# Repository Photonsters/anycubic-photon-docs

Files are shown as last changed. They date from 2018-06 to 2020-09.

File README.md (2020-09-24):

# Anycubic Photon Owner's Documentation

Use this repository to collect information on the Anycubic Photon LCD resin printer's hardware, software and usage. 

**IMPORTANT NOTE!**

**As of September 2019, Anycubic has been shipping printers which deceptively look like original Photon printers but are not. These new printers (commonly called the Fauxton) have new motherboards (PTB2BK) and are incompatible with the original Photon printers. The information provided here for the most part will not apply to this new printer.** 

**Please also note that most of the community tools, software, mods and information here do NOT apply to the new Fauxton or the Photon-S model. They are fundamentally different printers.** 

Want to help? Check at the bottom of this page for the [TO DO](#todo) list and open a [issue with #IWantToHelp.](https://github.com/Photonsters/anycubic-photon-docs/issues/new?title=IWantToHelp)

## Table of Contents

* [Frequently asked questions (FAQ)](FAQ.md)
* [Known issues](known-issues/photon-known-issues.md)
* [Photon technical specifications](#photon-technical-specifications)
* [Photon file image format](#photon-file-image-format)
* [Photon slicing software](#photon-slicing-software)
* [Community resin exposure settings](#community-resin-exposure-settings)
* [Community projects](#community-projects)
* [Community Mods](#user-mods-on-facebook)
* [Social media groups](#social-media-groups)
* [Models, Photon Blueprints & Resources](#models--resources)
* [Firmware Archives](/firmware/README.md)
* [TO.DO.](#todo)

<!-- toc -->

## Frequently asked questions (FAQ)
[Check the FAQ page](FAQ.md) before asking questions! You may find the answers to all your questions regarding setting up your Photon, to post processing your prints, already covered in the FAQ. 

## Known issues
There are several known issues with the Photon hardware and software. [Check the known issues page](known-issues/photon-known-issues.md) for details, solutions and workarounds.

## Photon technical specifications
#### Dimensions
- Machine Volume: 220(L)x200(W)x400(H)
- Print Volume: 115(L)x65(W)x155(H)
- Empty Vat weight 630g [(FB Link)](https://www.facebook.com/groups/AnycubicPhoton/permalink/1644848155659820/)

#### Photon masking
- RGB 5.5 MIPI_DSI 2K LCD screen [(Sharp LS055R1SX03)](https://github.com/Photonsters/anycubic-photon-docs/blob/dev/Temp-resources/LS055R1SX03-SKU958440.pdf) 
- 68.04(W)mm x 120.96(H)mm (5.46")
- XY resolution: 47.25µ (0.04725mm)
- 538ppi
- Color Pixel Arrangement:RGB Vertical Stripe
- Power Supply Voltage:AVDD=5.5+/-0.1V AVEE=-5.5+/-0.1 V
- MIPI 5.5 50 Pin 0.4 Pitch connectors: [Screen: WP7B-P050VA1 ; Board: WP7B-S050VA1 - (FB)](https://www.facebook.com/groups/AnycubicPhoton/permalink/1646286412182661/)

#### Motion driver / mechanics
- T8 leadscrew with 2mm lead/pitch
- Nema 17 Motor 1.8º 200steps/rev
- Driver embeded Polulu Alegro 4998 set at 1/16 microstepping
- Hardware resolution 10µ (0.01mm)
- Digital microstepped resolution 0.625µ (0.000625mm) - [Advised reading: Microstepping Myths and Realities](https://tinyurl.com/y92kexf5)

#### Electronics
- LED power 25W 405nm
- PSU 12v 6A (72w) - 5.5 x 2.5mm Jack - [check image](https://user-images.githubusercontent.com/11083514/42894729-92fd1f22-8aaf-11e8-9f58-2fdb9be91fb1.png)

#### Photon file image format
- 2560x1440px 
- Black and White 
- RLE 7bit encoding
- 538 dpi (537.566 dpi)

## Firmware & Configuration files
If you've just received your Photon, or it's working properly, **do not** update your firmware unnecessarily. 
- [Photon official firmware & default gcode](https://github.com/Photonsters/anycubic-photon-docs/tree/master/firmware) (including unofficial releases and gcode mods). Use at own risk. 

## Photon slicing software

#### [ANYCUBIC Photon Slicer](http://www.anycubic3d.com/support/show/594032.html)
Go to [this page](https://www.anycubic.com/) slicer will be shoved under the printer you will have to scroll a bunch.
 
 (https://www.anycubic.com/)

#### [**Chitu Slicer**](http://www.cbd-3d.com/en/soft/dlpslicer.shtml) (ANYCUBIC is rebranded Chitu)
Chitu devs have been helping Photonster devs with some support questions, and Chitu's new software release will allow for better integration of Photonsters tools with the slicer software, and will support many new formats including zip/gcode import/export.

#### [**Chitubox**](https://www.chitubox.com/) (New Slicer for the photon from the same makers of ChituDLP)
New software that integrates code and ideas first seen in the community projects VoxelOps, Validator, Rob's 3D photon Viewer and Photon File Editor Project. 

#### [**Photon Open Slicer**](https://github.com/Photonsters/Slicer) (Community developed OpenSource Slicer)
A independent command line Slicer from Photonsters, that can be integrated with MeshMixer or any other software capable of outputting a STL file. 

#### [List of Slicing Software](https://docs.google.com/spreadsheets/d/1wZFdewMztEp_1RPubQw_8UdIZK7Z2oIWxByVpAPAfXI/edit#gid=0)
Some of the slicers that are available to date.

## Community resin exposure settings
- [Known good resin settings](https://docs.google.com/spreadsheets/d/1crvzMnt_8NJXAsABinoIhcOjE8l3h7s0L82Zlh1vkL8/edit#gid=0) - Curated by Artur Fuste. 
- Also check the resin exposure finder test under community projects below.

## Community resin precision gauge test
[Resin Precision-Fit Test-Gauge](https://docs.google.com/spreadsheets/d/1yDwszgncTyOxvyJho6y1kxLJquH2GsfL83KaFXT6068) - This is for resin as tested with no software profile/compensation. Dimensions can be corrected by activating the horizontal-size compensation feature in your slicing software. If you don't have this feature, please contact your slicer developer.

## Printed material torsion test results
[Torsion Test Results](https://docs.google.com/spreadsheets/d/1JlqLSi4sxZLdA-hHCp6Ow4isoGMNI7nlE9Nmbj1ajWk) - 3D printed material comparison by torsion testing.

## Community projects
- [Resin Exposure Range Finder](https://github.com/altLab/photon-resin-calibration) - Quick method to test multiple resin exposure settings in one go. *(X3msnake)*
- [Photon File Validator](https://github.com/Photonsters/PhotonFileViewer) - Check if your sliced file has errors before printing. *(Bonosoft)*
- [Photon Voxel 3D Viewer](https://github.com/Ordenritterlein/PhotonTool/blob/master/README.md) - Javascript 3D model rebuilder and visualization from sliced Photon files. *(Ordenritterlein / Rob2048)*
- [Photon File Utils - PFE](https://github.com/NardJ/PhotonFileUtils) - Photon file visualizer editor and creator tools. *(NardJ)*
- [PCB2Photon](https://github.com/Reonarudo/pcb2photon) - Swift Gerber image to Photon for PCB mask burning and production. *(Reunarudo)*
- [Photon Go](https://github.com/Andoryuuta/photon) - Library to read and write Photon and .cbddlp files. *(Andoryuuta)*
- [UV light distribution tester](https://www.facebook.com/kzhkshj/posts/1782894801789685)
- [Pixel Dimming Tool](https://github.com/alpet83/PhotonProcessor)*(alpet83)*
- [Photon Open Slicer - POS - Meshmixer Plugin](https://github.com/Photonsters/Slicer) - *(NardJ)*
- [Voxel Ops](https://github.com/Photonsters/VoxelsOps) - Voxel tools to dilate, erode, hollow, project and measure. *(Antharon)*
- [DecreasePixel GUI](https://github.com/Hans2004/Anycubic-Photon-decreasePixel-with-GUI) - Simple erode function. Compensate slices on .photon files to closely fit design dimensions. *(Hans De Jong)*
- [DecreasePixel CLI](https://github.com/Hans2004/AnyCubic-Photon-Decrease-Pixel) - Same as the above but Command Line version. Confirmed working without issue [in a FB post](https://www.facebook.com/groups/AnycubicPhoton/permalink/1835060846638549/) *(Hans De Jong)* 
- [cbddlp - xycompensate](https://github.com/yaqwsx/ElegooMarsUtility) *(yaqwsx)* - [check his blog](https://blog.honzamrazek.cz/)
- [Hexeditor Okteta](https://github.com/Hans2004/okteta-photon) template for .photon format. *(Hans De Jong)*
- [PRUSA SLICER SL1 files to Photon Converter](https://github.com/fookatchu/SL1toPhoton) *(fookatchu)*
- [pyPhotonfile - library for photon file manipulating](https://github.com/fookatchu/pyphotonfile)*(fookatchu)*
- [cbddlp, photon, photonS, pws - File cross converter](https://github.com/Ordenritterlein/PhotonsFileConverter) *(Ordenritterlein)*
- [PNG2Photon - Convert a image to a photon file](https://github.com/0x3f00/PhotonCpp) *(0x3f00)*
- [Photon Timelapser EOS](https://github.com/lagnajeet/PhotonTimeLapse) [video](https://www.youtube.com/watch?v=u1mt8Q_h7qg&list=PLVMKVuHiQBM1TjSq00kHshXuMJEsih7rn&index=18) *(lagnajeet)*
- [Photon Network Controller - Allows to manage files and start prints on any CBD board printer](https://github.com/Photonsters/Universal-Photon-Network-Controller/blob/master/README.md) *(lagnajeet)*
- [Gcode to Images](https://github.com/svsdval/gcode2photon) *svsdval*
- [PhotonPCB - Create printed circuit boards with MSLA](https://github.com/borelg/PhotonPCB) *(borelg)*
- [UV3DP - Multiformat converter command line tool (PHZ,CTB,CBDDLP,CWS(nova),SL1...)](https://github.com/ezrec/uv3dp/blob/master/README.md) *(ezrec)*

- [**#BlackBoaProject** - Photonsters Rebuild Improvement and Documentation of a Photon Classic](https://photos.app.goo.gl/FDa5uVDD6zWR39Wt8)

## User mods (on Facebook)
- [Cheap and easy Heater, PTC Fan and temperature controller](https://www.facebook.com/groups/AnycubicPhoton/permalink/1550627681748535/)
- [PTC Heater and temperature controller V2](https://www.facebook.com/permalink.php?story_fbid=10157191752823680&id=651553679)
- [PTC Heater and temperature controller that prints flat with no support](https://www.thingiverse.com/thing:3412516?fbclid=IwAR2-71wrzMquMxCCqnwgRDSsMIfEYvs9tsWgYu_tbYqgjgc3luOuuhr0QFU) 
- [Printed Universal resin drainer](https://www.facebook.com/groups/AnycubicPhoton/permalink/1508547859289851/)
- Gangsta resin drainers [1](https://www.facebook.com/groups/AnycubicPhoton/permalink/1376704139140891/), [2](https://www.facebook.com/groups/AnycubicPhoton/search/?query=gangsta%20drainer&epa=SEARCH_BOX)
- [Red & Black Acrylic windows with cad files](https://www.facebook.com/groups/AnycubicPhoton/permalink/1367548836723088/)
- [Tuning Photon Z driver or using a external Driver module](https://www.facebook.com/media/set/?set=oa.1350659371745368&type=3)
- [Anycubic Photon Z Axis Modification](https://www.facebook.com/groups/AnycubicPhoton/permalink/1599717403506229/) 
- [IPA Cleaner Station with stir Mixer](https://www.facebook.com/groups/AnycubicPhoton/permalink/1604847169659919/)
- [IPA Classic Cleaning Station](https://www.facebook.com/permalink.php?story_fbid=10157258442468680&id=651553679) 
- [Pi Zero W WiFi Thumb Drive](https://www.facebook.com/groups/AnycubicPhoton/permalink/1610232152454754/)
- [Pi Zero W WiFi Thumb Drive 2](https://www.facebook.com/groups/AnycubicPhoton/permalink/1640913006053335/)
- [NanoDLP Photon Brain Transplant](https://www.facebook.com/groups/AnycubicPhoton/permalink/1657220444422591/) 

**NETWORK ENABLED PHOTON UI**
- [PSHCNET UI in action](https://www.facebook.com/groups/AnycubicPhoton/permalink/1651711838306785/)
- [Network Ready back grill vent](https://www.thingiverse.com/thing:3613864)

**Z AXIS MODS**
- [Dual Rail Solid - skipbaker](https://www.thingiverse.com/thing:3539028/files)
- [Dual Rail Flanges - PhotonHebs](https://www.thingiverse.com/thing:3473868/files)
- [Dual MGN9H Printed - Beezen](https://www.thingiverse.com/thing:3504872)
- [Dual Linear Bearings - danroh](https://www.thingiverse.com/thing:3490431)

## Social media groups
- [Anycubic Photon LCD Printer Owners Group](https://www.facebook.com/groups/AnycubicPhoton/?ref=group_header) on Facebook, with over 10,000 members. 
- [ANYCUBIC Photon Forum](http://photonforum.statusavailable.pt/viewforum.php?f=23), managed by official distributor PT. 
- [Twitter #AnycubicPhoton](https://twitter.com/hashtag/ANYCUBICPHOTON?src=hash)

## Models & resources

### Calibration models
Use these resources to test how your Photon is printing, and to remove guesswork from calculating resin exposure times.
- [X3msnake's Resin Exposure Range Finder](https://github.com/altLab/photon-resin-calibration)
- [ANYCUBIC Photon calibration file By Ilja](https://www.myminifactory.com/object/3d-print-anycubic-photon-calibration-file-70127)
- [Photonia Pixel Perfect Range Tester](https://www.facebook.com/groups/AnycubicPhoton/permalink/1567794123365224/) 
- [Photon LCD mask Boundary Checker](https://www.thingiverse.com/thing:3345921) - A printable test for your mask boundaries, which may vary from printer to printer.
- [Bed of nails UV coverage test](https://www.thingiverse.com/thing:2852334) - A quick test print to check for even UV coverage of your build plate. Useful for full plate prints or models placed close to edges. 
- [Photon LCD defect mapper](https://www.thingiverse.com/thing:3395800) - A quick test print to map LCD dead pixels, and workaround them in your slicer. 
- [Z Wobble quick test](https://www.facebook.com/groups/AnycubicPhoton/permalink/1507962279348409/) - A quick test for Z wobble, or other planar surface anomalies. 

### Photon Cad files and Blueprints
- [Photon Blueprints CAD files on this repo](https://github.com/altLab/anycubic-photon-docs/tree/master/photon-blueprints)
- [Photon on Thingiverse](https://www.thingiverse.com/search?q=Anycubic+Photon)

### Models for Resin Printing
- [DLP/SLA models on MyMiniFactory](https://www.myminifactory.com/search/?tech=DLP_SLA)

### Tutorials, videos, tips & tricks
- [Photonsters Youtube Channel](https://www.youtube.com/channel/UCtkUaPjl49fyaNOLNTbKHlQ)
- [Troubleshooting DLP Prints](https://l3d.ie/2018/06/29/dlp-3d-printing-troubleshooting/)
- [Supports created with Meshmixer](https://youtu.be/OXFKVmMwXCQ?t=2m10s)
- [How supports work](./Resources/AddingSupportsForSLA3DPrinters-v1.pdf)
- [2018 - Resin Casting: A Collection of Hypotheses](http://www.santafesymposium.org/2018-santa-fe-symposium-papers/2018-resin-casting-a-collection-of-hypotheses)
- [How to use Netfabb supports with LCD printers](https://docs.google.com/document/d/1aC4MIkIyjG61bllVglCZ308qukxOhE7jJ9tKQQh0aPY)
- [How LCDs work](www.bitly.com/HOW-LCDS-WORK)
- [The science behind a 3d Printer - Projection, Mask and Resins](https://youtu.be/97ARLiTHjX0)

## TODO
1. Videos for the [Photonsters Youtube Channel](https://www.youtube.com/channel/UCtkUaPjl49fyaNOLNTbKHlQ)
1. Map Photon hardware
1. Map Photon file anatomy
1. How-to test resins
1. How-to level
1. How-to use external Stepper driver
1. Create Repo with resins and community consensus resin test method [check this page](https://github.com/Photonsters/anycubic-photon-docs/blob/master/resin-tests/resin-testing-protocol.md)
1. List official slicers and alternative/usefull software
1. Collect config files and firmware from Google group
1. Collect community reversed Photon CAD parts
1. List community software projects and tools for the Photon
1. Finish compare chart https://ethercalc.org/ResinPrintersCompareChart

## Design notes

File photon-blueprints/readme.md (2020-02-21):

# PHOTON BLUEPRINTS

Serial connection: 115200, 8, n, 1
You can use Putty, Tealterm or Arduino Serial

- Touch - SPI (SCK, SDI, SDO, CS, GND, 5V)
- Touchscreen LCD - Paralell 16bit (D0-D15, RS, WR, RD, CS, GND, 5V)
- [BlackBoa Dissasembly photos and mesures](https://photos.app.goo.gl/FDa5uVDD6zWR39Wt8)

- [CAD model of complete Photon mechanical assembly on GrabCAD](https://grabcad.com/library/photon-3d-printer-assembly-1)

## ICs

Screen Controllers

- XPT2046 or HR2046 (touch - all screens)
- [ILI9341 (2.8")](2.8inches_V3.9_Back_Dimensions.PDF) 
- [ILI9488 (3.5")](3.5inches_V3.9_Back_Dimensions.PDF) 
- [TSC2046 - Touch Digitizer IC](https://www.ti.com/lit/ds/symlink/tsc2046.pdf)

- [TouchScreen Pinouts (KUDOS Cex123)](Photon_Touchscreen_Pinouts.pdf) 
- Touchscreen cable: 40-Pin FFC/FPC Flat Cable Pitch 0.5mm 300mm [Forward Direction](https://user-images.githubusercontent.com/11083514/60126474-fea23a80-9785-11e9-896a-7aaa8cd2b04f.png)

Logic Chips
- [FPGA - Altera EP1C3 Cyclone 1](https://user-images.githubusercontent.com/11083514/60964874-5e631e80-a30c-11e9-8678-4eee115b1eeb.jpg) (responsable for image processing)
- [ARM - STM32F407ZCT6](https://user-images.githubusercontent.com/11083514/60965063-cdd90e00-a30c-11e9-8cb0-f4535a3e73f8.png) (responsible for motion actions and ui)

## OTHER PARTS

- Omron endstop [EE-SX674-WR](https://s.click.aliexpress.com/e/_d6Iysd5)
- Z axis U ballbearings [SG15-2RS](https://s.click.aliexpress.com/e/_d7qVfIT)
- [List of all fastener sizes and threads used on the Photon](https://github.com/Photonsters/anycubic-photon-docs/blob/master/photon-blueprints/Anycubic%20Photon%20Fasteners%20Sheet.xlsx)

#### Confirmed Gcode Commands via Serial:

- M6030 "Photon/AA-TEST-PRINTS/_ShallowAnglesAATest_0X.photon" (starts a print file name imeddiatly)
- M6032 "Photon/AA-TEST-PRINTS/_ShallowAnglesAATest_0X.photon" (Reads a File Into Memory to be started with M6045) R: (file length in bytes)
- M24 (Starts printing the M6032 open file on memory)
- M27 (Report SD print status) (M27 S4 - Report 4 seconds, M27 S0 - Stop reporting, M27 C - Report currently open filename)
- M6045 I4000 "M24" (Waits the Delay set time and Starts Printing the M6032 open file on memory)
- M4001 (returns the configured stepper movement for all axis) R: (X:0.011430 Y:0.011430 Z:0.000625 E:0.001340 T:0/0/0/155/1 U:'GBK' B:1) 
- M105 (returns sensor temperatures) R: (ok T:161 /0 B:164 /0 @:0 B@:0)
- M8512 "configFile.gcode" (Dumps the current config.gcode EEPROM data into a file)
- G28 Z (Home Z Axis)
- G0 Z10 (Move Z axis at max speed)
- G0 Z10 F600 (Move Z axis at F speed)
- M6040 I100 (Reboot I defines the delay before restart)
- M7506 I636264 T0		//0; 1; color_flip, (Changes UI colours Negative/Positive/or switch watever its on)
- M9005 '"Networkname","Password"'
- G90 Absolute Positioning
- G91 Incremental Positioning

[List of WIFI commands taken from ChituClient App](ChituClientWifiProtocol-translated.txt)

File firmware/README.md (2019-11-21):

## ANYCUBIC PHOTON FIRMWARE ARCHIVE 

These are archived firmware images of the Anycubic Photon printer.

Unless there is an issue with your machine or current firmware, it is recommended that you do not unnecessarily update or reflash it. 

**The latest firmware as of October 2019 available from Anycubic's website is v4.2.19. This version is buggy and not recommended. Use v4.2.18 instead.** 

*By downloading and using the archived files, you acknowledge that you are doing so entirely at your own risk.*

[Yes, I understand, show me the files!](https://github.com/Photonsters/anycubic-photon-docs/tree/master/firmware) 

## List of Known Firmware
The stock firmware of most of the first generation blue windowed machines is 4.0.11_LCD. It is the only firmware that did not have the "frame shearing" bug. This bug was finally addressed and fixed on firmware v4.2.18.  

Here is a partial list of known firmware with images as documented on a 
[Facebook post.](https://www.facebook.com/groups/AnycubicPhoton/permalink/1599259826885320/)

---

## General Instructions

- Copy the 3 files (sometimes only 2) to the USB root folder.
- On startup the update.lcd file will be used to update the firmware and the printer will start and then beeps.
- At this point, navigate via the touchscreen menu to the choose and "print" the other file(s), consecutively.  
- Once done, safely shutdown and **delete the firmware files** from your usb stick. 
- Now you can restart the printer. 

If the menu shows a T_88 error code, this means that the firmware files were not coherent.
Check in the menu if the version has been updated to the correct firmware version, if so you can "print" the other two files again.

---

## Photon GCode Commands 

Big thanks to Master Johnson Yeh for putting this together.

*Translated text:*

After getting the Chinese version of the gcode parameter description, let me know better that the experiment I did before is correct.

If you want to control the relevant parameters of the Z axis, the following parameters can be used together with the application.

M8070 S3 is set to the slow rise Z distance height of the release type.

M8070 Z6 is the total height of the Z release type = S# slow rise Z distance height + fast rise distance height, so the height of 6-3=3 rapid rise is 3mm

M8015 T2 is the speed of Z-axis slow release
M8016 T3 is the rapid rise and rapid descent speed of Z-axis release. This parameter speed controls the speed of rapid rise and rapid decline.

I would like to suggest that Anycubic should add a new parameter to control the falling speed parameter.

After finalizing the settings, you need to save the parameters you designed to the device using the M8500 parameters.

My last test parameter was parameter(Slow T1).gcode changed as follows:

M8015 T1;

M8016 T2;

M8070 Z6;

M8080 S3;

M8500 ;

*Original text:*

取得中文版gcode參數說明後, 讓我更明白之前做的實驗是正確的.
如果要控制Z軸的相關參數有下列幾個參數是可以搭配應用的.

M8070 S3 是設定離型的慢速上升Z距離高度
M8070 Z6 是Z離型總高度 = S#慢速上升Z距離高度+快速上升距離高度, 所以6-3=3快速上升的高度為3mm

M8015 T2 是Z軸慢速離型上升的速度
M8016 T3 是Z軸離型快速上升及快速下降速度, 這個參數速度控制著快速上升跟快速下降的速度

我想建議 Anycubic 應該新增加一個參數在控制下降的速度參數.

最後完成設定後, 需要使用Ｍ8500參數將您所設計的參數保存到設備內.

我上一次測試參數是 parameter(Slow T1).gcode 更改的內容如下:

M8015 T1
M8016 T2

M8070 Z6
M8080 S3

M8500

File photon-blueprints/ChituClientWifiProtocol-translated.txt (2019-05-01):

G:\yiyu\workspace\software_v3_V1.2.30\software_v3_V1.2.30\software_v3\DOC\赤兔主板-wifi通信协议-wifi-protocal.txt 26 November 2016 16: 35
Author: Yi Yu last modified: 2016 1 14
Requirements:motherboard firmware must > V1. 3. 7
Support for androi, ios
Communication method: UDP protocol, 3000 ports
Communication mode：
Mobile terminal: send command
Device side: successful return ok\r \ \ n
Some commands will also display additional information before, if not specifically indicated, the success only return ok \ r\n, otherwise return the relevant information and then return
Back to ok\ \ r \ \ n
Failure returns Error:+ error message\r\n
All the commands are based on the handshake operation, in the face of G28 this long operation command, it is recommended to set the longest probably 5s socket ultra
When, once timed out, sends the M4004 command to query the current status
Basic commands：
M99999
Local Area Network broadcast, through this instruction to scan the device
ok MAC:18:fe:34:d7:a7:16 IP:192.168.1.106 VER:V10. 0. 3 ID:38, d9, 5d, fa, dd,8b, 1a, 4d
NAME:yiyu-esp1
MAC:wifi mac address
IP: WiFi LAN IP address
VER: version number of the wifi firmware
ID: unique identification of the wifi module
NAME: set WiFi module name
Get the device's xyze step parameters, step parameters will be used in subsequent file compression.The first command after the connection must be this
All the commands that you can't follow are unresponsive!!!!!!!!!!!!!!
M4001
ok. X:0.0127 Y:0.0127 Z:0.00125 E:0.00225 T:0/200/200/200/1 U: 'UTF-8'B:0
# T after the parameters for the machine type / x Stroke / y stroke / Z stroke / nozzle number 0: xyz Model 1: delta model
, For delta models, x-Stroke=y-stroke=delta radius parameter Z for delta Z maximum debugging
#U is connected to the back of the motherboard coding, B: followed by whether to enable the hot bed
Get status:
#This command must be issued once about 2S, if there is no status message for a long time, the motherboard side may be disconnected
M4000
Return:
ok. B:-50/0 E1:-52 / 0 E2: 76/0 X:0.000 Y:0.000 Z:0.000 F:0/0 D:0/0/0 T:0
B: hot bed current temperature / target temperature
E1: thermal Head 1 current temperature / target temperature
E2: thermal Head 2 current temperature / target temperature
X, Y,Z:coordinate position, in mm
F: Extrusion Head 1 fan PWM / extrusion Head 2 fan the maximum value is 256
D: SD ocation of card currently Read/ total size of file currently read on SD card / whether pause
, When the file is not open, the total size is 0, the pause flag is only valid when the file is open, and 1 is paused
T: when the file has started, only the file starts printing is valid
Move command:
X axis plus G0 X10 F1200 I0 \ r \ \ n #X axis moves right 10mm, at a speed of 1200mm/s per minute movement
X axis minus G0 X-10 F1200 I0 \r \ \ n
Y axis plus G0 Y10 F1200 I0 \r \ n
Y-axis minus G0 Y-10 F1200 I0 \r \ n
Z axis plus G0 Z10 F600 I0 \r \ n
Z-axis minus G0 Z-10 F600 I0 \r \ \ n
E axis plus G0 E10 F300 I0 \r \ \ n
E-axis minus G0 E-10 F300 I0 \r \ \ n
HOME zero G28\r \ \ n
Heating extrusion head Command:
M104 S60 #heated to 60 degrees, followed by S is the temperature of the degree of execution
Heating hot bed command:
M140 S60 #is heated to 60 degrees, followed by S is the temperature of the degree of execution
-1.-
G:\yiyu\workspace\software_v3_V1.2.30\software_v3_V1.2.30\software_v3\DOC\赤兔主板-wifi通信协议-wifi-protocal.txt 26 November 2016 16: 35
Fan on.:
M106 S127 #fan on, PWM is 127, maximum is 256
Fan off:
M107
Emergency stop.:
M112 #stop all the motors
Extended Command:
Display the file list: / / note transcoding, sent up must be m4001 information returned encoding
M20
Normal returns the following results, the board will return a line by line：
Begin file list\r\n #
First file 34343\r\n #file name file size (bytes)
Second file 34233\r \ \ n
End file list\r \ n #end of file list
Select the SD card and print: / / note transcoding, the file must be sent down m4001 encoding information returned
M6030 'file name' #such as M6030 ' file.gcode'
Start or resume printing:
M24.
Pause printing:
M25
Stop printing:
M33.
Create file: / / note transcoding, the file must be sent down m4001 information returned encoding
M28 file name#such as M28 new_file.gcode
In the case of the file is not closed(such as printing), return Error!File: test.gcode is opened\ \ r \ \ n
,Where"test.gcode " is the name of the file that has been opened
Delete file: / / note transcoding, the file must be sent down M4001 information returned encoding
M30 file name#such as M30 new_file.gcode
Write the file：
After the M28 file is created
All commands except the M4000 and M29 are treated as write data, and the effective data length of a package is recommended to be 256 * 5 or
Shorter
The data written is formatted as follows：
/ Valid data (data length) / data in the file offset (4byte)|
Test (1byte, XOR operation of all preceding data) / 0x83(1byte) |
If an incorrect test or data loss occurs, you receive the following message:
resend 32432\r\\ N where 32432 is the offset of the data to be retransmitted in the file
If a write error occurs, it will receive:
Error:write dat\r\ \ n
Write the end of the file:
M29.
Read files:
M6032 'file name' #such as M28 'new_file.gcode'
Successful return ok L: file length, such as ok L:3128340
Failure returns Error:.....
Then request data read out with M3000 request data read out, the data format of the data format to write the file when the return of the same
If the data is lost, request the retransmission of the data at the specified file offset with M3001 Ixxx, such as M3001 I324242
Turn off the device, after printing the shutdown module of the device, the command will let the device power off：
M4003
Querying the current command blocking condition：
M4004.
In

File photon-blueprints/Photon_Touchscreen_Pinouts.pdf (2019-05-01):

### 2.8 inch LCD pinout (LCD connector)

ILI9341 controller

FPC 40pin 0.5mm pitch (bottom contacts)

n/c = not connected

pin | function
1 D0
2 D1
3 D2
4 D3
5 GND
6 VCC
7 /CS
8 RS
9 /WR
10 /RD
11 n/c
12 Touch XR (X+)
13 Touch YD (Y+)
14 Touch XL (X-)
15 Touch YU (Y-)
16 Led A (backlight anode) 17 Led K1 (backlight catode 1) 18 Led K2 (backlight catode 2) 19 Led K3 (backlight catode 3) 20 Led K4 (backlight catode 4) 21 FMARK
22 D4
23 D8
24 D9
25 D10
26 D11
27 D12
28 D13
29 D14
30 D15
31 /RESET
32 VCCA
33 VCC
34 GND
35 D5
36 D6
37 D7
38 n/c
39 n/c
40 n/c

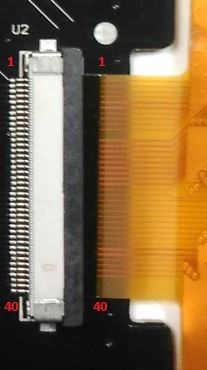
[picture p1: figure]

Photon LCD pinout (touchscreen module and mainboard connectors)

ILI9341 lcd controller

XR2046 SPI touch controller

FPC 40pin 0.5mm pitch (bottom contacts on touchscreen PCB and top contacts on mainboard)

n/c = not connected

* = not fully confirmed

pin | function
1 3V3
2 3V3
3 3V3
4 5V (n/c on 2.8 module)
5 5V (n/c on 2.8 module)
6 GND
7 GND
8 GND
9 D7
10 D6
11 D5
12 /RESET
13 Touch CLK
14 Touch /CS
15 Touch DIN
16 Touch DOUT
17 Touch /PENIRQ | (n/c on mainboard*)

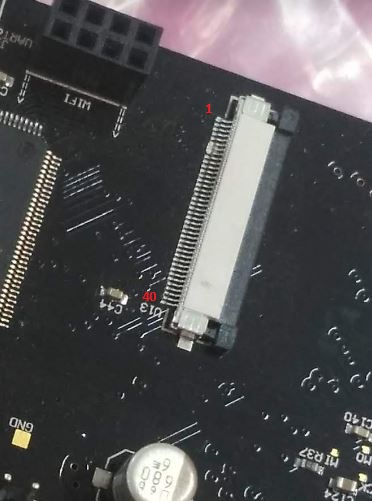
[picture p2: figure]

18 D15
19 D14
20 D13
21 D12
22 D11
23 D10
24 D9
25 D8
26 D4
27 Backlight control
28 /RD
29 /WR
30 RS
31 /CS
32 D3
33 D2
34 D1
35 D0
36 GND
37 n/c*
38 n/c*
39 n/c*
40 3V3

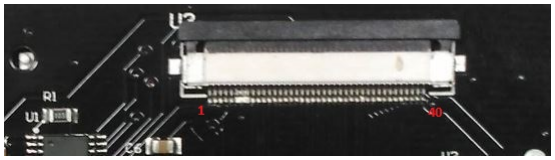
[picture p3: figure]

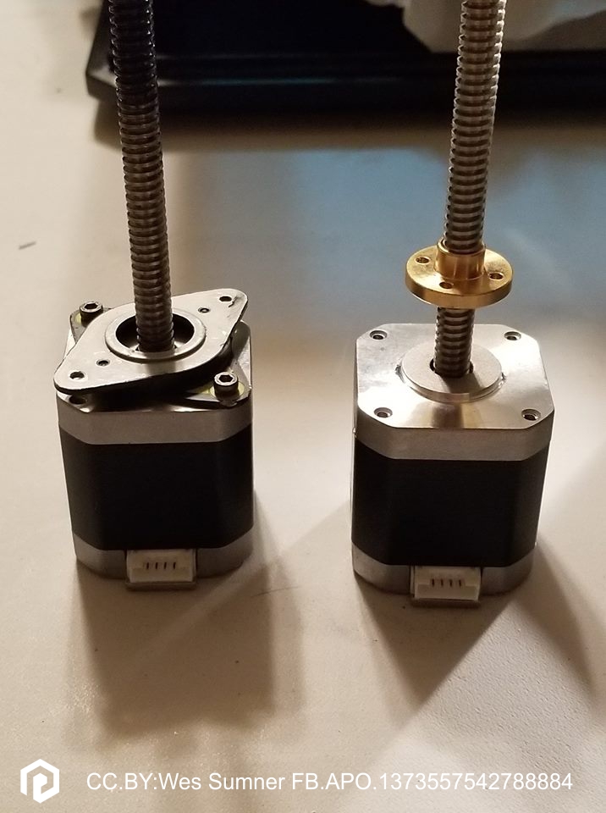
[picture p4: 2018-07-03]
hardware/photon-stepper-motor.jpg

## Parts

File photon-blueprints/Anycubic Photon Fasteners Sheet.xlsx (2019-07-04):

Fasteners used for Anycubic Photon printer
Description | Qty | Thread | Length (mm) | Head Style | Head Hex (mm) | Notes
Bottom Case Screws | 6 | M3 x 0.5 | 5 | Socket Head Cap Screw | 2.5 | 4 around bottom perimeter, 2 inside through red platform
Acrylic Window Screws | 28 | M3 x 0.5 | 3 | Button Head Cap Screw | 2
Rubber Feet | 4 | M6 x 1.0 | 12 | Rubber Foot
Hinge Screws | 8 | M3 x 0.5 | 8 | Countersunk Socket Hex | 2
Vat Thumb Screws | 2 | M4 x 0.7 | 12 | Knurled Thumb Screw |  | 12mm diameter thumbscrew
Z axis mount to Rail Block | 4 | M5 x 0.8 | 30 | Socket Head Cap Screw | 4 | Stainless, fully threaded
Main Platform Plate Mount Screws | 4 | M3 x 0.5 | 8 | Socket Head Cap Screw | 2.5 | 2 at inside front corners, 2 through rear face of enclosure
Vat holdown bracket mount screws | 4 | M3 x 0.5 | 12 | Socket Head Cap Screw | 2.5 | Screwed from bottom of platform, 2 per bracket
Z Axis top plate screws | 2 | M4 x 0.7 | 8 | Socket Head Cap Screw | 3 | Stainless
Homing fence screws | 2 | M3 x 0.5 | 5 | Socket Head Cap Screw | 2.5
Brass lead nut mount screws | 4 | M3 x 0.5 | 12 | Socket Head Cap Screw | 2.5
Homing fence set screw | 1 | M4 x 0.7 | 4 | internal hex head | 2 | threaded from bottom up in z axis block
Stepper motor platform mount screws | 2 | M3 x 0.5 | 12 | Socket head cap screw | 2 | two, mounted diagonally
Stepper motor isolator mount screws | 2 | M3 x 0.5 | 5 | Socket head cap screw | 2 | two, mounted diagonally
Z axis rail to platform mounting screws | 4 | M4 x 0.7 | 20 | Socket head cap screw | 3 | stainless
Homing limit light mount screws | 2 | M3 x 0.5 | 8 | Socket head cap screw | 2.5
Mainboard bracket to platform screws | 2 | M3 x 0.5 | 8 | Socket head cap screw | 2.5
Mainboard to mainboard bracket screws | 2 | M3 x 0.5 | 18 | Socket head cap screw | 2.5
DC-DC driver board screws | 2 | M2 x ? | 12 | Socket head cap screw | 1.5
LED/Heatsink to reflector scrws | 4 | M3 x 0.5 | 8 | Socket head cap screw | 2.5
Reflector to platform screws | 4 | M3 x 0.5 | 5
Build plate knob screw thread | 1 | M6 x 1.0 | 22 | all-thread |  | All-thread M6 rod with divot for set screw
Build plate knob set screw | 1 | M4 x 0.7 | 6 | set screw
Build Plate Screws | 11 | M3 x 0.5 | 12 | Countersuck Socket hex | 2
Vent fan screws | 2 | M3 x 0.5 | 16 | Button head | 2
Touchscreen to case | 4 | M3 x 0.5 | 4 | Socket Head Cap screw | 2
Case fan mounting screws | 4 | M3 x 0.5 | 16 | Socket head Cap Screw | 2
Case fan nuts | 4 | M3 x 0.5 |  | hex
Build plate set screw | 1 | M6 x 1.0 |  | internal hex

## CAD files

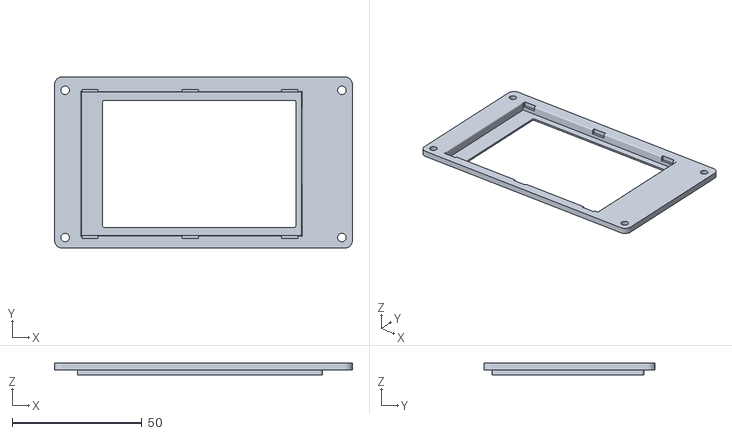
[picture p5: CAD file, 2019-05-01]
photon-blueprints/LCD-COVERS-STL/lcd_cover_3.5.STL
115.0 x 66.1 x 4.60

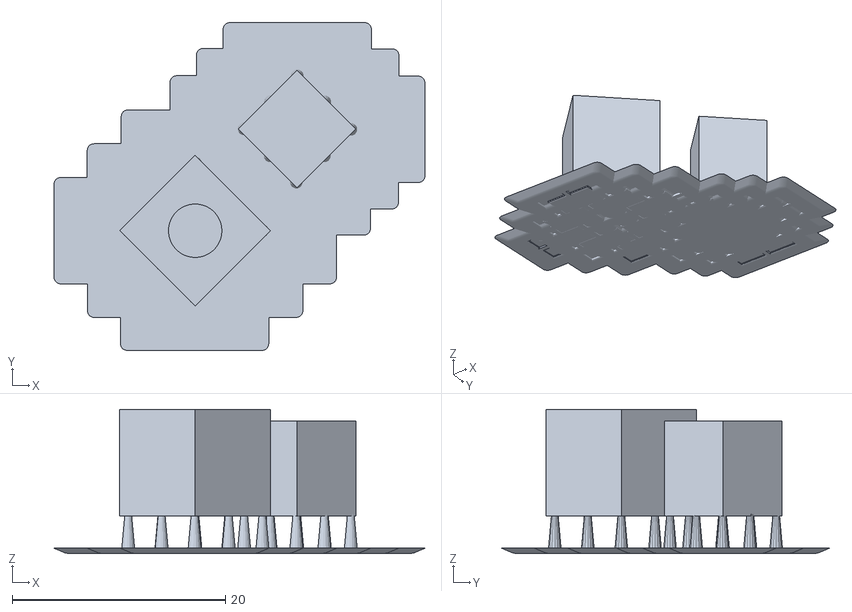
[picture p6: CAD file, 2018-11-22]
temp/nestacube_10mm_.stl
34.8 x 30.7 x 13.5

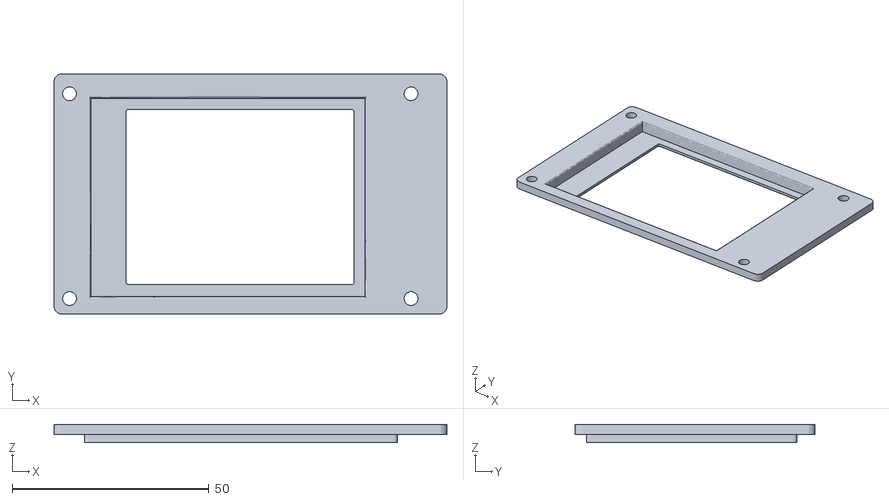
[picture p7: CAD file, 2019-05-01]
photon-blueprints/LCD-COVERS-STL/lcd_cover_2.8.STL
100.0 x 61.1 x 4.60

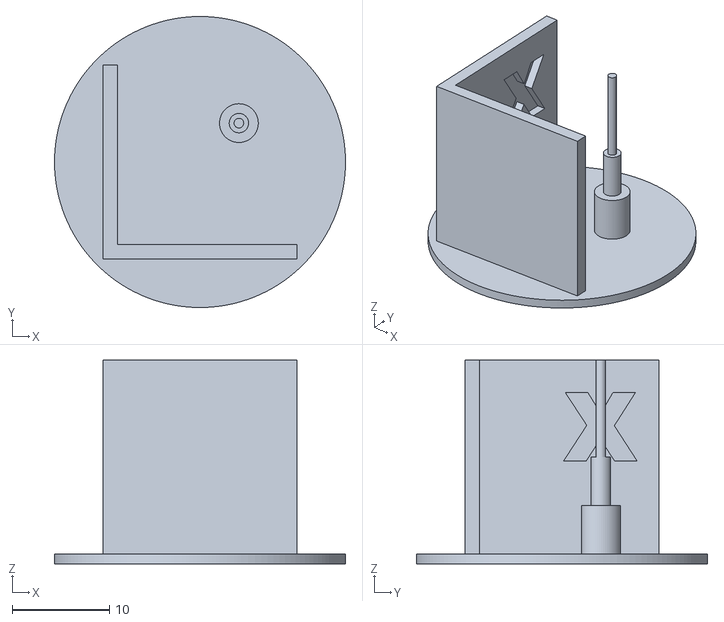
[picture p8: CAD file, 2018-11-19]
temp/notacube_01a_.stl
30.0 x 30.0 x 21.0

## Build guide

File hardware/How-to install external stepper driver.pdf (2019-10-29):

## AnyCubic Photon

## External Stepper Driver Installation

Special Thanks to:
Photonsters Facebook Group

## Table Of Contents:

- Disclaimer
- Why?
- Parts list
- Procedure
- Advanced settings
- Appendix

## Caution/Disclaimer

- This will likely void your warranty. Do not attempt if you aren’t comfortable with a soldering iron, multi-meter, and possibly breaking your Photon
- Read everything first
- Don’t blame me or anyone else if you break your printer.

## Why?

- Internal stepper driver is limited in function
- External stepper driver can:
- Lower noise of stepper motor
- Increase reliability and repeatability
- Increase mechanical smoothness of Z-axis
- External stepper will not:
- Increase physical vertical resolution
- This is function of the leadscrew and stepper motor
- Mechanical limits vertical resolution to multiples of 0.01mm
- Eliminate Z-wobble
- Make prints stick to your bed

## Parts list

- Materials
- Stepper driver of your choice
- Selection is outside of scope of this document, I used BigtreeTech TMC2208 DIY
- Stepper driver breakout board
- 0.1” (2.54mm) header pins (male-male)
- 3 female-female jumper wires for header pins
- 1 female to male jumper wire
- 2 male to bare wire jumper wires
- Some way to mount the breakout board
- I used 3mm screw, nut, and 3d printed spacer.
- Tools
- Soldering iron with good tip for precision work
- Not required if using press-fit header pins
- Tools that came with your Photon
- Precision Jewelers screwdriver set

## Parts list

Parts I used and links:

Header pins (10 pack of 40) - AliExpress (http://s.click.aliexpress.com/e/BPvcGSda) eBay (https://www.ebay.com/itm/NEW-10-pcs-40-pin-single-row-pin-header-2-54mm-pitch-length-10cm-black-color/163878052694)
Stepper Driver (BigTreeTech TMC2208 – Select the DIY one) – AliExpress (http://s.click.aliexpress.com/e/ncC8glkU) eBay (https://rover.ebay.com/rover/1/711-53200-19255-0/1?campid=5338601725&toolid=20008) Stepper Breakout board – AliExpress (http://s.click.aliexpress.com/e/tAUJD1hI) eBay (https://rover.ebay.com/rover/1/711-53200-19255-0/1?campid=5338601725&toolid=20008)
Jumper wires (select the one that comes with F-F, F-M, and M-M) – AliExpress (http://s.click.aliexpress.com/e/E5yLH97K) eBay (https://rover.ebay.com/rover/1/711-53200-19255-0/1?campid=5338601725&toolid=20008) Screw Set (3mm screws + nuts) – AliExpress (http://s.click.aliexpress.com/e/4UMHqCiU) eBay (https://rover.ebay.com/rover/1/711-53200-19255-0/1?campid=5338601725&toolid=20008)
Spacer – Printed (3.5mm id, 8mm OD, 6.35mm tall) – Thingiverse (https://www.thingiverse.com/thing:3891866)
Jewelers Screwdriver set – AliExpress (http://s.click.aliexpress.com/e/3hgAUcGs) eBay (https://rover.ebay.com/rover/1/711-53200-19255-0/1?campid=5338601725&toolid=20008)

## Procedure:

1. Remove motherboard
2. Install new pin headers on motherboard
3. Wire stepper driver breakout board
4. Install stepper driver and setup
5. Test & change direction if required
6. Set Vref on new driver
7. Reinstall everything

## Step 1: Remove motherboard

- See official AnyCubic YouTube video https://www.youtube.com/watch?v=Denj5z8BtLg
- When disassembling machine, position build platform support near the middle.
- Notes:
- Newer photons may be slightly different than video
- Be very careful when removing ribbon cables for screen and front touch screen
- You may need to remove some hot glue from the green screw terminal connectors and double sided tape from the LCD mask connector.

## Step 2: Install headers on motherboard

- Will be installing two sets of pins – one to pull the signal from the motherboard, and another to give the breakout board 5V
- Additionally, will be running 12V and GND from the main power connector to the breakout board
- Pins can be solder or pop-in type – pictured are solder type

## Step 2: Install headers on motherboard

- Male standard header pins, 0.1” (2.54mm) spacing
- One set of 3 (or 4) and one single pin
- Set of 4 required if you pull GND connection from the stepper mirror header, 3 if you pull GND from the power connector
- Recommended to pull GND from the power connector directly

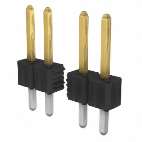
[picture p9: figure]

Solder style
header pins

Push in style
header pins

## Step 2: Install headers on motherboard

- Install 3 (or 4) set into holes labeled ‘Z’ on motherboard
- Install 1 additional pin in 5V connection in UART ports near USB slot
- Solder in place from back of board if required

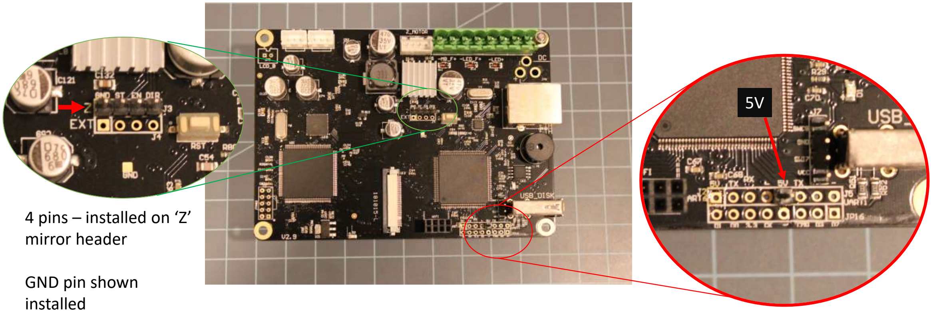
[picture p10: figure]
4 pins – installed on ‘Z’ mirror header; GND pin shown installed

## Step 3: Wire stepper driver breakout board

- For ease it is suggested to use breakout board built for stepper drivers
- 6 wire connections total
- If using breakout board you will need:
- 3 female to female jumper wires
- 1 (or 2) female to male jumper wire
- 1 (or 2) male to bare wires
- Depends on where you want to get ground

## Step 3: Wire stepper driver breakout board

- There are 6 wire connections to make on the stepper driver board
- 3 are to the Z-mirror pin headers installed in step 2 to control the stepper driver – these are labeled as:
Function | Motherboard | Breakout Board
Enable | EN | E
Step | ST | S
Direction | DIR | D
- Using female to female jumper wires, make the following connections:
- EN pin to the E pin
- ST pin to the S pin
- DIR pin to the D pin.

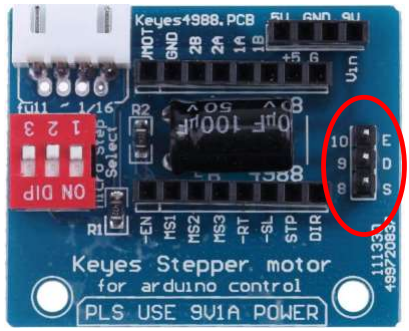
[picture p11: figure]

## Step 3: Wire stepper driver breakout board

- To give the power to breakout board – 3 more
connections are needed
- 12V, 5V, and GND
- For the GND connection, you have two options:
- Option 1 – connect directly to screw terminal from power source using male to wire jumper wire
- This is what is shown
- Option 2 – connect to the Z-mirror pin header labelled GND
- Option 1 is recommended
- Connect wire end of male jumper wire to 12V screw terminal with red wire coming from the switch. Connect this to the 9V pin on the breakout board
- Connect one male to female jumper to the 5v line on the breakout board and wire to the 5V pin on the motherboard

## Step 3: Wire stepper driver breakout board

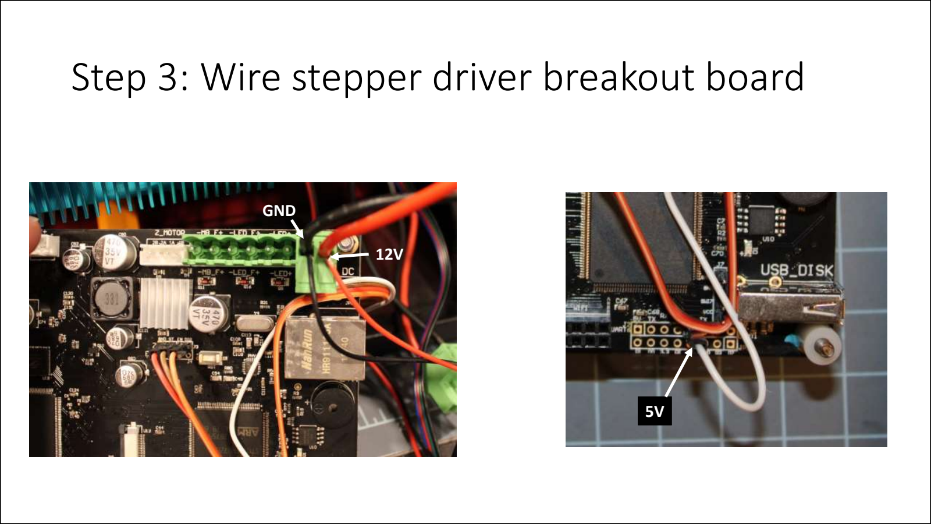
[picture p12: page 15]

12V

GND

5V

## Step 3: Wire stepper driver breakout board

- 12V, 5V, and GND wires connected to breakout board.
- Either Pin labeled GND is okay
- Engage, Direction, and Step wires connected

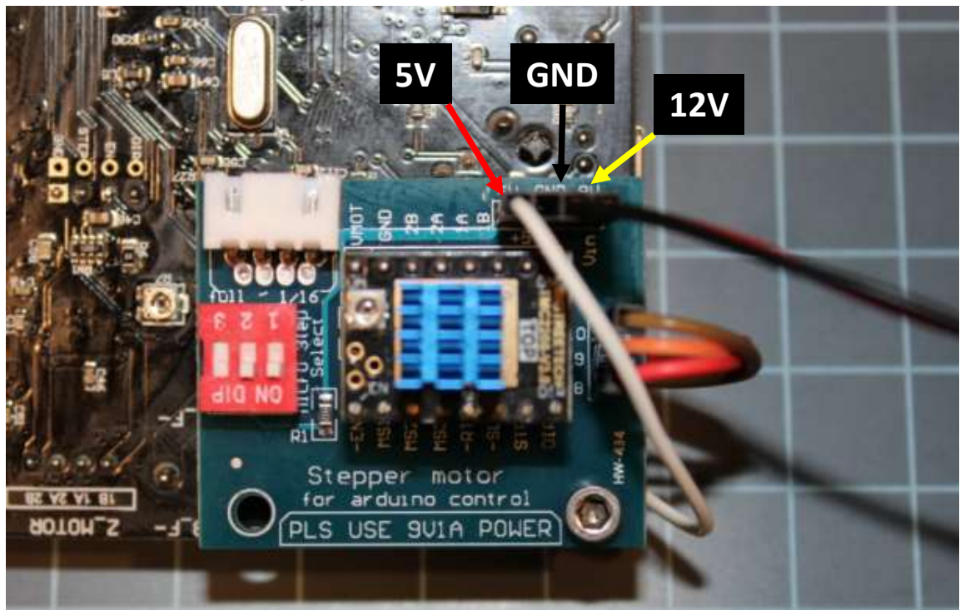
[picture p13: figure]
GND

## Step 4: Install stepper driver & setup

- Install the stepper driver into the breakout board
- Ensure proper orientation. Your driver should have pins labeled – plug into matching pin on the breakout board
- Example - EN driver pint to EN breakout board pin

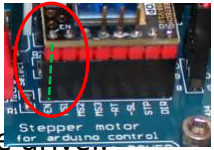
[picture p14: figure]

- The switches on the breakout board are for setup for the driver.
- Follow the manual/spec sheet for your driver to set MS1, MS2, and MS3 to the correct settings
- Example settings on next slide – confirm yours in spec sheet for your stepper driver.
- Install heatsink if provided with stepper driver

## Step 4: Install stepper driver & setup

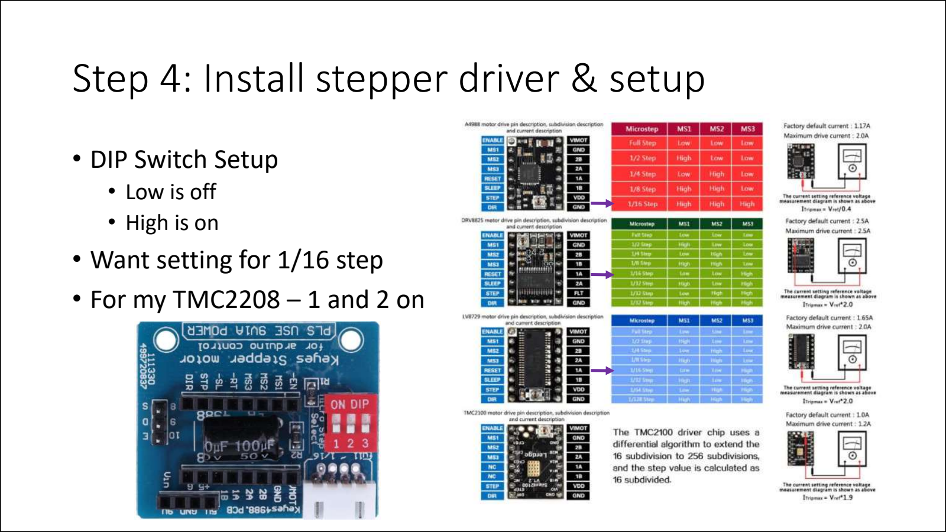
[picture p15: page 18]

- DIP Switch Setup
- Low is off
- High is on
- Want setting for 1/16 step
- For my TMC2208 – 1 and 2 on

## Step 5: Test & change direction if required

- Reconnect power to motherboard (leave machine unplugged for now)
- Reconnect touch-screen LCD
- Connect motor to the breakout board (not back to the motherboard)
- Ensure all connections to breakout board and motherboard are correct
- Only connections required are 6 wires to breakout board, power to motherboard, and LCD touchscreen ribbon cable
- Plug in and turn machine on
- Try not to touch anything other than power switch and touchscreen LCD when the machine power is on.
- Using the ‘Tools’ menu – attempt to move the Z-axis up and down to check direction.

## Step 5: Test & change direction if required

- If direction is correct (e.g. up moves the platform up) – congrats!
- Proceed to Step 6 to set the Vref
- If direction was backwards (pushing up arrow moved the platform down) we have to change direction of the stepper – Go to Step 5b.

## Step 5b: Changing stepper direction

- This method will cover changing the wiring for the stepper motor to switch direction
- This can also be done in the gcode - see advanced section
- Involves de-pinning the connector, swapping two wires, and putting them back in.
- Turn off and unplug printer
- Unplug connector running from breakout board to the stepper motor

## Step 5b: Changing stepper direction

- Take 1.4mm wide screwdriver and gently push down on tab on pin in the stepper motor connector while pulling on wire at same time
- Remove two wires that are next to each other
- I removed red and blue
- Switch the pins, reinstall into connector, and reconnect to stepper breakout board

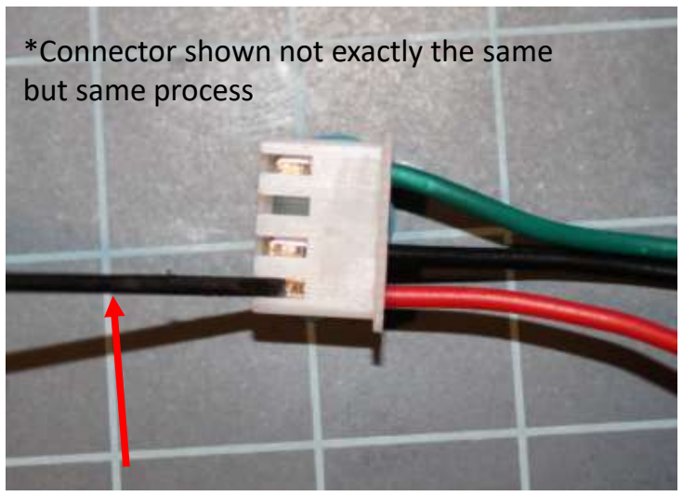
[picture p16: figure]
*Connector shown not exactly the same but same process
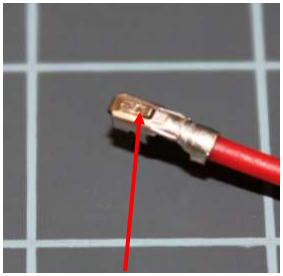
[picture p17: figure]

1.4mm wide screwdriver | Tab to push

Red and blue wires switched and reconnected

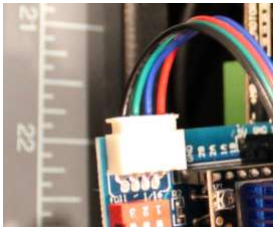
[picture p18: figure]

## Step 6: Set Vref on stepper driver

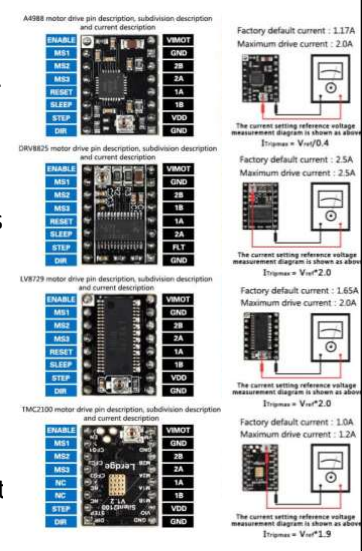
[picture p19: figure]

- Vref is set by small screw potentiometer on stepper driver
- Correct voltage and procedure varies based on stepper driver
- See driver spec sheet for instructions and voltage requirements
- Stepper motor is 1.5amp max current (1.06amp RMS current)
- Use this value to set max voltage on the stepper driver
- Go low and test – lower current keeps stepper motor cooler and will last longer
- For my TMC2208 driver – Vref was set to 1.15V (max Vref of 1.4)
- Examples of some common steppers drivers shown on the right

## Step 6: Set Vref on stepper driver

- With machine plugged in and power on- use multi-meter to check voltage at points indicated by your stepper driver spec sheet
- On TMC2208 – I used GND pin and the top of the potentiometer to check
voltage
- Adjust voltage using potentiometer as required to get to spec.
- Turn off and unplug machine between each test | Negative lead

Positive lead

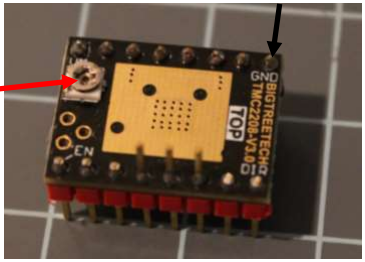
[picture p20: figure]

TMC2208 Stepper Driver

## Step 7: Reinstall everything

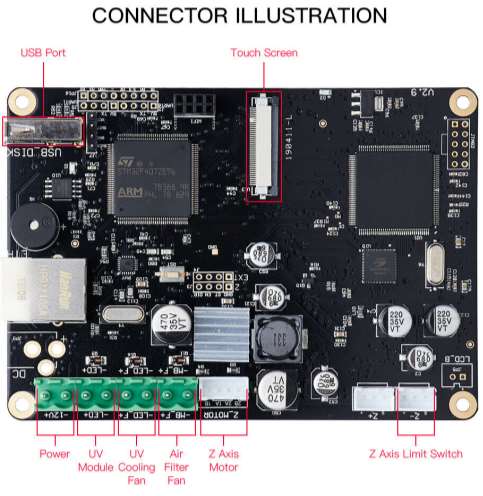
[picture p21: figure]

- Find good mounting location for your breakout board
- Be careful to not let the back touch any metal components or the motherboard
- I used a spare hole in the motherboard and a 6mm spacer for mounting
- Reinstall motherboard and reconnect wiring
- Reference AnyCubic video
- Test again
- Complete reassembly

## Advanced Settings

- Stepper reversal
- Stepper motor direction can be switched by g-code, rather than flipping polarity on a coil. To do this, you will need to make a new gcode file and print on your printer.
- Make a new file, and include the two lines below, exactly as the are.
M8004 I1
M8500
- Save as a new file with the extension .gcode
- Put this file on a USB and print on your printer.
- Check to ensure Z-direction switched
- To change it back, simply change the file to say the following: M8004 I-1
M8500
- For more details on the gcode – check the Photonsters GitHub (https://github.com/Photonsters)
- Direct Link to the factory defaults g-code w/ translations – HERE (https://github.com/Photonsters/anycubic-photon-docs/blob/master/firmware/factory-defaults-translated.gcode)
- If you flash your firmware – this value will reset back to default

## Appendix: Various pictures of installation

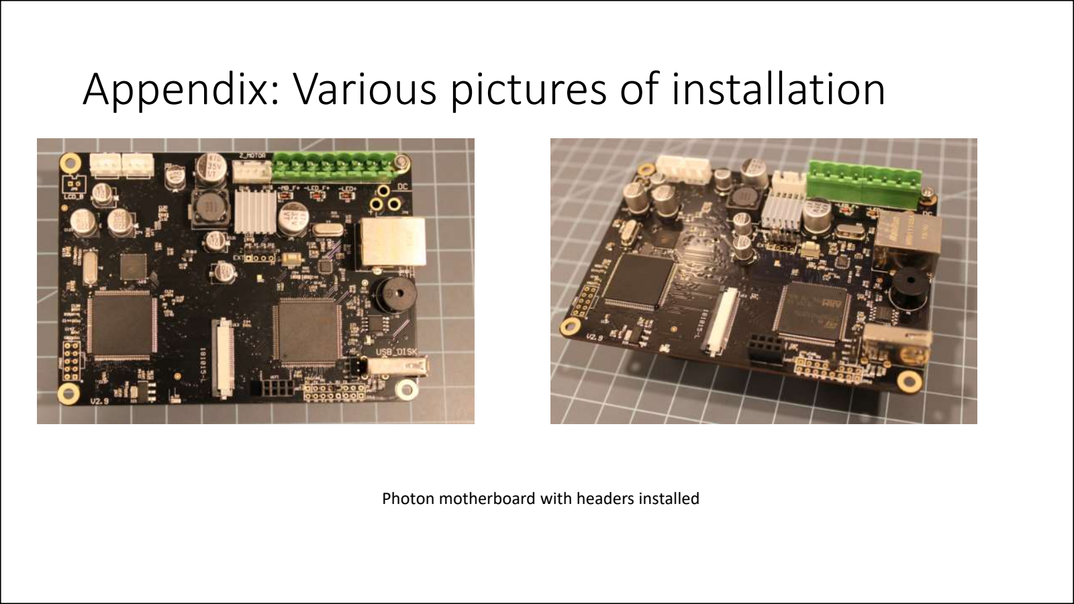
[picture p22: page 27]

Photon motherboard with headers installed

## Appendix: Various pictures of installation

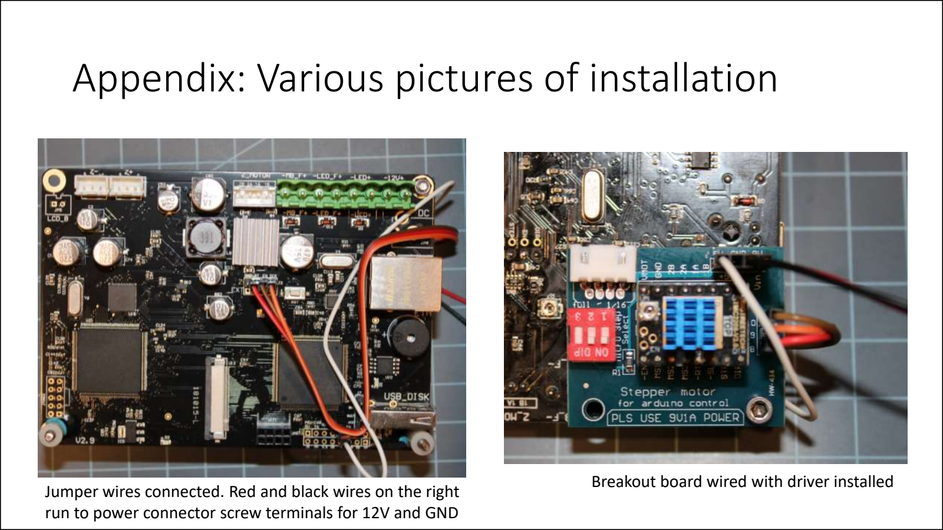
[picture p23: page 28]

Jumper wires connected. Red and black wires on the right run to power connector screw terminals for 12V and GND

Breakout board wired with driver installed

## Appendix: Various pictures of installation

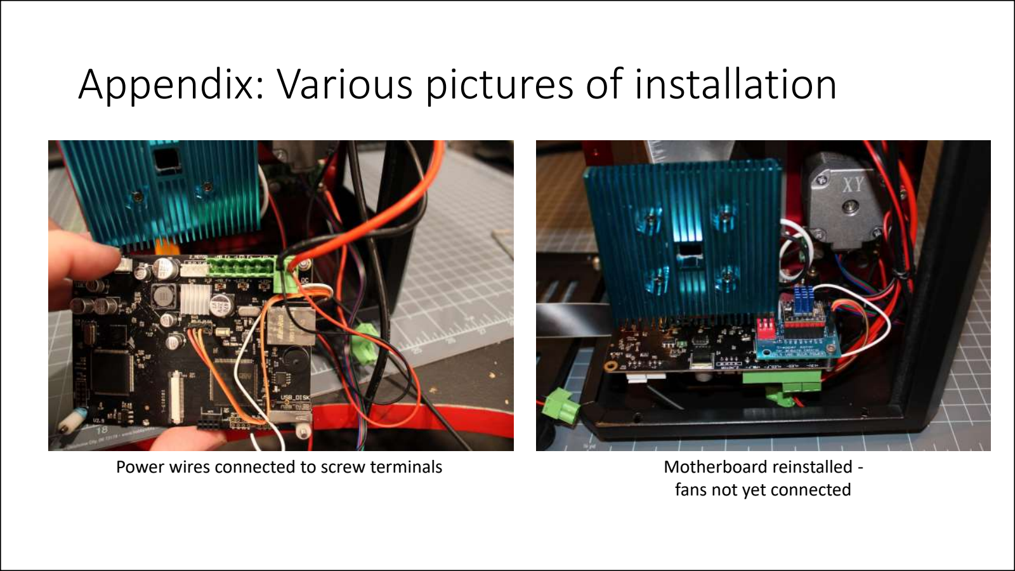
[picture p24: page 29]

Power wires connected to screw terminals | Motherboard reinstalled - fans not yet connected

## Appendix: Various pictures of installation

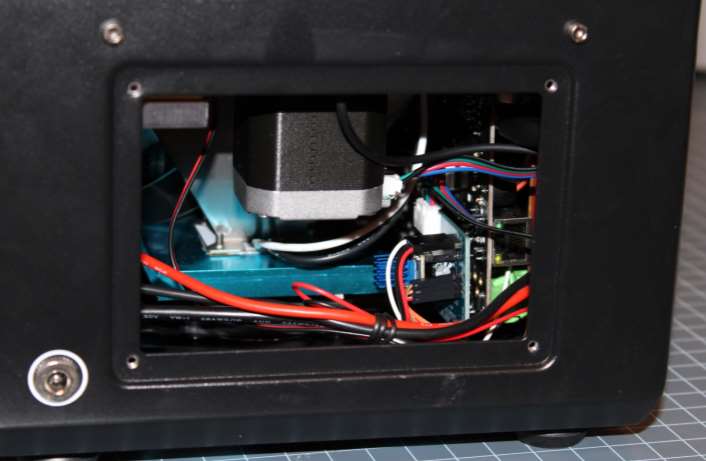
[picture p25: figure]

Reassembled – view from rear

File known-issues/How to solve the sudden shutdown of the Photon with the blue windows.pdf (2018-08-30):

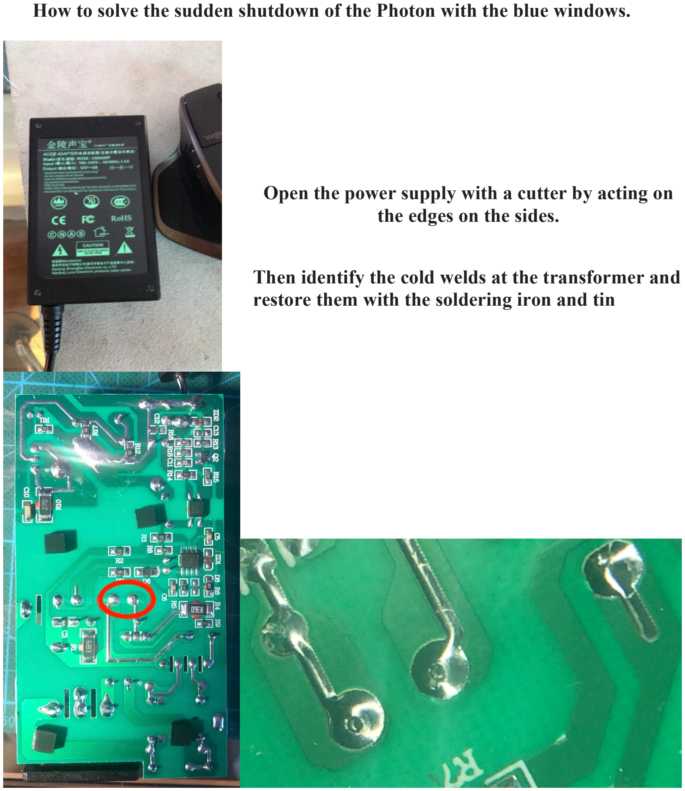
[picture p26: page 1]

How to solve the sudden shutdown of the Photon with the blue windows.

Open the power supply with a cutter by acting on the edges on the sides.

Then identify the cold welds at the transformer and restore them with the soldering iron and tin

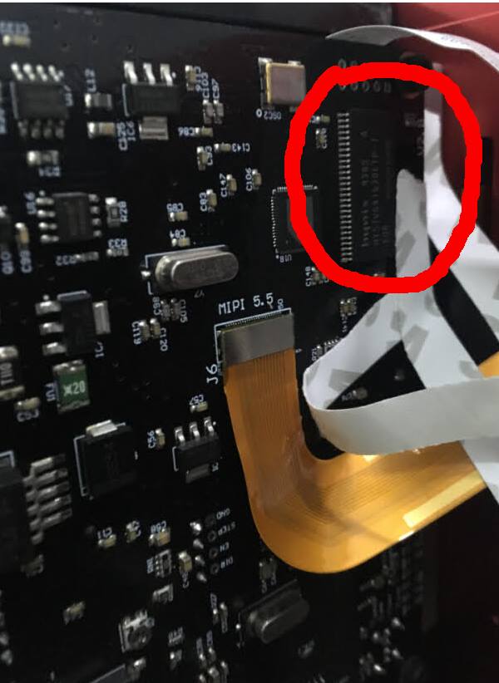
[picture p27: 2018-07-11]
known-issues/LCD-issues-mainboard-soldering-defect.jpg

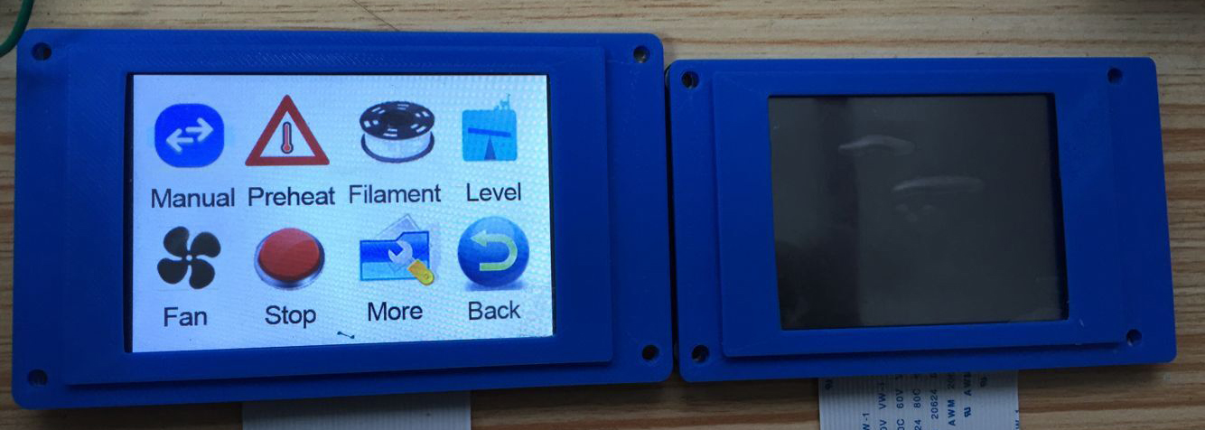
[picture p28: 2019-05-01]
photon-blueprints/LCD-COVERS-STL/LCD-PrintedCovers.jpg

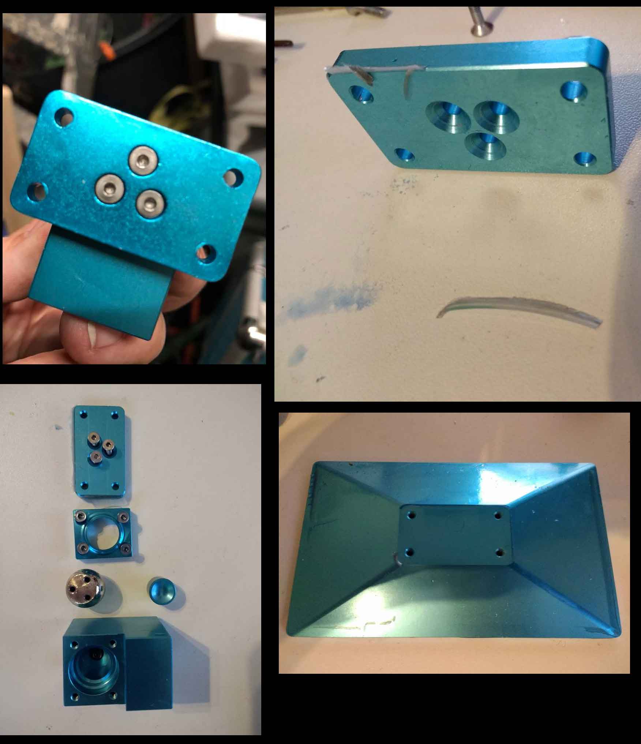
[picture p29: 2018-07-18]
known-issues/photon_bed_mount_assembly.jpg

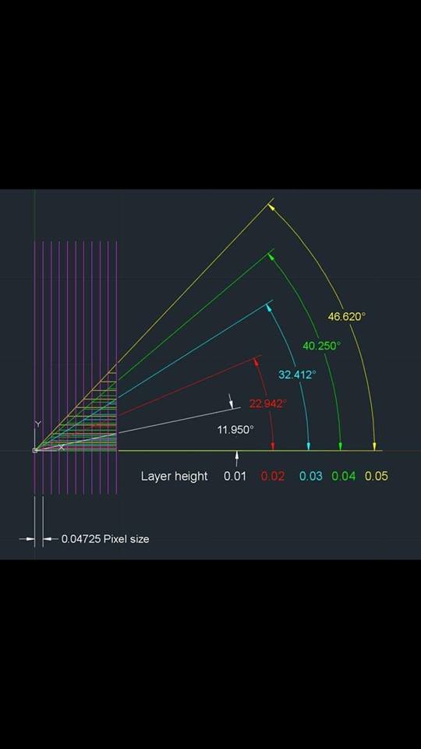
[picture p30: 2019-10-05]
Resources/layer height vs print angle.jpg

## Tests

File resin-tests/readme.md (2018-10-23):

## Resin testing and reviews have it's own project now

- Check [resin-reviews.org](http://resin-reviews.org) project

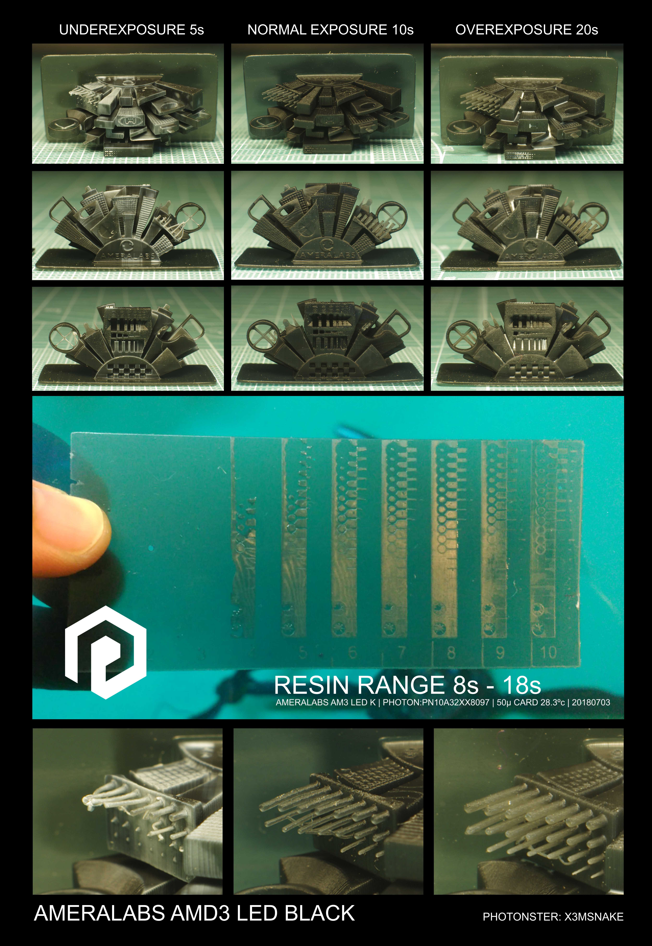
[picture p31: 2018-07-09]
resin-tests/Ameralabs-AMD3-Black-180709-x3msnake.jpg

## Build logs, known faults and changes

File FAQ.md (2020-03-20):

# Frequently Asked Questions
Frequently asked questions regarding the Anycubic Photon LCD Printer and SLA-LCD resin printing in general. 

## In September 2019, Anycubic started shipping a look-alike of the original Photon (Classic). 
Without any prior announcements, **Anycubic quietly started to ship these machines to unsuspecting buyers. These new printers look exactly like the original Photons (with steel bodies and yellow windows) but are not. The motherboard has been changed, making them an entirely different printer that only looks like the original.** 

These look-alike Photons (commonly called Faux Photons or Fauxtons) share the same mainboards (PTB2BK) with the Photon-S and could then only print new *.pws files as they had Photon-S mainboards,  making them incompatible with the original Photons.  

Due to community outcry, in early November 2019 Anycubic were finally forced to admit that they were indeed shipping these Fauxtons. In an official announcement on their Facebook page, they apologised for the "confusion" their ambiguity caused and clarified that they were still shipping the original Photons side by side with the lookalike Fauxtons and that buyers would have to specify their preferred versions. Since then, the new Fauxtons (and the Photon-S) received firmware updates allowing them to print original Photon files. 

As of mid-November 2019, all Photon printers shipping from China are the new Fauxtons. Last remaining stocks of the original Photon were still being shipped only from NA and European warehouses. 

### How can I tell if my original Photon (Classic) is a true original or the new Fauxton? 
Unfortunately, since the Fauxton look physically the same as the original Photon, the only way to tell is to check the firmware version or check the motherboard inside. Look-alike Fauxtons ship with firmware version v3.x.x or v5.x.x). 

### I'm considering buying an original Photon, I see there are Blue, Yellow, Orange and Red windows versions, what's the difference? 
All newer original Photons and new Fauxtons look-alikes come with Yellow windows. Older original Photons (prior to August, 2018) had Blue windows. Blue [doesn't block UV well](https://www.facebook.com/groups/AnycubicPhoton/permalink/1287895011355138/) and they were changed to yellow later, with newer firmware, slight revisions to uncap the top end of the Z lead screw and include a better PSU. 

Machines with Orange or Red windows are basically user mods. 

### Can I print my original Photon (Classic) files on the look-alike Fauxton? 
Originally, the file formats were incompatible. Since the November 2019 firmware update for the Fauxton (and the Photon-S), original Photon files can now be printed on the new Fauxton. This post on the Photon Owners Group provides [details the confusing state of the various different file formats (before the Fauxton firmware update).](https://www.facebook.com/groups/AnycubicPhoton/permalink/1821580714653229/) 

### What about the differences between the original Photon (Classic) and the Photon-S?
The Photon-S was released in February 2019, supposedly as an interim upgrade to the original Photon. However, it turned out to be a sidegrade, rather than a true upgrade. Due to the different motherboard, it's actually a completely *different* printer altogether. 

When first released, the fundamental difference was that the S model was not file compatible with the original Photon, and thus could not use any of the original print files sliced for the original Photon. With the November 2019 firmware update, it can now print original Photon files although initial user reports say compatibility is buggy.  

**Do note that many of the [essential community software and tools](https://github.com/Photonsters/anycubic-photon-docs/blob/master/README.md#community-projects) that have been developed for the original Photon are not compatible and do not work with the S model (or new Fauxton).** 

Contrary to many misleading online reports, when first released, the S model [did **NOT** have anti-aliasing (AA) 
](https://www.facebook.com/groups/AnycubicPhoton/permalink/1616230841854885/) while the original Photon had this important feature via an unofficial firmware and an official AA firmware update in May 2019.

In August 2019, Anycubic finally released a new firmware for the S model which included the AA feature, but with the update the file format was changed from *.photons to *.pws and made it incompatible. It also broke Chitubox slicer support for the previous file format. At that point, no other slicer (except for paid ones) supported the new *.pws format. Since the November 2019 firmware update, compatibility has been restored. 

The hardware, software and cosmetic differences are:
- Anycubic motherboard instead of the tested and proven Chitu CBD-Tech motherboard. 
- Anycubic slicing software instead of Chitu CBD-Tech slicer. Photon-S sliced files cannot be printed on original Photon, and vice versa. 
- Plastic shell/chassis instead of all metal stamped steel chassis. 
- Two column guide sliders on the same central Z lead screw instead of a single column slide. (Note that these are just simple sliders on guide rods, not recirculating bearing linear rails.) 
- Exposure unit consists of a 38W 4X7 UV LED lensed array instead of a 25W 4X4 UV LED reflector cone source. 
- Dual "filtration" units instead of a single unit. These are useless marketing gimmicks and just spread smell. 
- 10mm taller print capability on the Z axis. 
- Build plate surface is machined flat after texture blasting and blue anodizing, otherwise exactly the same. 
- Most other components such as the LCD, vat, build plate, carriage arm, etc., remain exactly the same. 

Disassembly and [internal photos (FB link)](https://www.facebook.com/groups/AnycubicPhoton/permalink/1609289172549052/) of the Photon-S by Michael Morairty. 

### I've just bought a Photon, what accessories should I get? 
- [What you need before printing](http://makerfun3d.com/toolbox-resin-printers) by Kevin Rank. (Note that the UV curing suggestion, while usable, is not of the optimal 405nm wavelength required).  
- [Here's a video](https://youtu.be/OqJIF1E7MIg) showing some of the basic accessories needed, plus how to filter resin and vat cleaning by Garret Bertrand. 
- You will also need a known good branded USB stick (beware of fakes), formatted FAT32. **The included usb stick is known to be problematic and prone to eventual failure.** Transfer all the files from it to your known good USB stick and use that instead. 

### I've just received my new Photon, should I update the firmware first? 
No, it's not necessary, and not recommended at all. Set your printer up and do the test print first. Make sure that your Photon is functioning as it should before considering doing any firmware updates. 

**Do not update** if your Photon is working well. If you're running older firmware and need AA functionality, **do not update to version v4.2.19** as that version is [buggy](https://www.facebook.com/groups/AnycubicPhoton/permalink/1755649334579701/), it is recommended to use v4.2.18 instead. 

## Table of Contents

* [SAFETY](#safety) 

* [BUILD PLATE TRAMMING (LEVELING)](#build-plate-tramming-leveling) 

* [VAT & FEP SETUP](#vat--fep-setup) 

* [MODEL SETUP & SETTINGS](#model-setup--settings) 

* [PRINTING](#printing) 

* [CLEANING](#cleaning) 

* [POST PROCESSING](#post-processing) 

* [TROUBLESHOOTING](#troubleshooting) 

* [MAINTENANCE](#maintenance) 

* [WARRANTY](#warranty) 

* [ACKNOWLEDGMENTS](#acknowledgments) 

<!-- toc -->

## SAFETY

### Before you start printing, remember, **safety first!** 
It is highly recommended to handle all resins as though they are toxic unless you have specific documentation which states otherwise.

- 3D printing resins are photopolymers, they react with light especially UV. The process is exothermic and produces very high heat. 
- If resin gets into your eyes, or on your skin and is exposed to light, bad things will happen. 
- Ensure that you are wearing eye protection. You do not want to get resin into your eyes. 
- Ensure you are wearing chemical-resistant gloves, nitrile or neoprene. Latex is not recommended unless only for short periods of time. 
- If you get resin on your skin or clothes, keep away from direct sunlight and wash with soap and water immediately. Do not wait! 
- Do not directly inhale or ingest resin. 
- Common sense applies. 

## BUILD PLATE TRAMMING (LEVELING) 

### What's this leveling that I keep hearing about?
Incorrect build plate tramming (levelling) is the number one reason for print failures. It is a statistical fact, most of the issues posted on the [Anycubic Photon Printer Owners Group](https://www.facebook.com/groups/1194619320682708) invariably traces back to imperfect build plate leveling as the root cause. 

- **Make sure you take the time to level your build plate correctly.** Do not rush this step in your hurry to start printing.
- Once your build plate is leveled correctly and locked down tight, you do not have to relevel it anymore unless you make other adjustments that affect the build plate. 
- Ensure that you lock down the build plate after leveling. **Lock that setting (grub) screw tight.** 
- Do not confuse build plate tramming (leveling) with adjusting the 4 legs of the machine.

### So how do I tram (level) my build plate? 
It is highly recommended that you use the official method aka paper method if you're using standard FEP film thickness (100~200um). 

Only try the Flint Read method if you're having trouble getting your build plate level with the paper method, or you're experimenting with thinner FEP film. 
- [Paper method (official) by Anycubic - Youtube](https://youtu.be/bIMwjmVl3Ho?t=2m32s)
- [Paper method by Nick Williams - Youtube](https://youtu.be/qEaNVfT8y9w)
- [Flint Read method - Youtube](https://www.youtube.com/watch?v=roAqm5c3rfU) Be very careful if you try this method as you could scratch the FEP film or [pressure damage your LCD screen.](https://www.facebook.com/groups/AnycubicPhoton/permalink/1760625187415449/) 

Important notes: 
- Press Home to bring the build plate down before starting to make build plate leveling adjustments. If you do not Home first, it will not set Z=0 correctly. 
- After setting Z=0 verify that it is set correctly by removing the vat and starting a print (aka dry run), put a piece of paper on the screen and check that the build plate starts the first layer at the correct Z=0 position that you have set. 
- Remember that Z=0 is not the same as Home.

### How tight to the paper should I tram/level the build plate?
If you are using the recommended paper method, the paper should be tight enough to pull out with even resistance but not able to push back in. Remember that the build plate must grip the paper evenly. 

**Remember** that as you tighten the setting (grub) screw it will move the plate down a tiny fraction more. You will find that you cannot pull the paper anymore, so you should raise / backoff the build plate level by 0.1mm (100um) until the plate is gripping the paper with even resistance, and that you can pull but not push it back. Then only set Z=0.
- [Example leveling video - Youtube](https://youtu.be/Y0bz5nYwll0)
- [Tight but not too tight example - Youtube](https://youtu.be/qEaNVfT8y9w)
- [Detailed Anycubic leveling instructions - Youtube](https://youtu.be/bIMwjmVl3Ho?t=2m32s)

### What type of paper should I use to level the build plate? 
Just regular photocopy paper, they're generally around 80gsm, but any paper 70 ~ 120gsm (average thickness ranging from 0.05 to 0.10mm) should work too. Just ensure that the paper is clean and not creased or folded. 
Do note if you're using thinner than standard FEP film, the paper method may not work well. Use Flint's method instead. 

### I tried to tram the build plate but one side is tighter than the other? 
Using your fingers, push the opposite side of the plate when tightening the grub screw. Alternatively, if you're using the paper method, you can slip another strip of paper to the side which is too tight and then tighten the screw. You may need to try this a few times to get perfect level. 

### I tightened the build plate as much as possible but it's still loose? 
- If no matter how much you tightened the grub screw to lock the build plate down and the plate still moves, remove the grub screw and check if there's another one already in the hole. Remove the extra screw and retighten. 
- The screws holding the build plate assembly together may be loose. [Disassemble, check and retighten.](https://github.com/Photonsters/anycubic-photon-docs/blob/master/FAQ.md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) 

### I set Z=0 but when I press Home the position is different?
**Home is not Z=0!** Home is fixed, it is the hardware Z endstop, unless you change it physically, it will always be the same position. Z=0 is the offset distance between Home and your screen, you define it when you level the build plate, that's why you have to Home first then move the platfrom, then set Z=0. 

When a new Z=0 is specified, pressing Home will NOT move the platform to the position you specified, it will be the start position when a real print actually starts. You can check it by removing the vat and starting a print. (Thanks to Philippe Maegerman for the original explanation.) 

### Do I have to relevel my build plate after every print? 
No, it is absolutely not necessary. If you have correctly leveled and then tightened and securely screwed and locked down the build plate tight, it will remain in place and correctly leveled for a very long time. 

Make sure you have really tightened the setting (grub) screw to lock the build plate. You only need to relevel your build plate if it has slipped or been knocked or you made changes that affect the Z=0 position. 

### Should I sand my build plate?
Are you using speciality castable resins? If yes, see below. 

If not, then it is absolutely **NOT NECESSARY** at all. Contrary to all the claims and misinformation being repeated that sanding away the blue anodized colour solves adhesion problems, it does not. 

When you have correctly leveled, the blue anodized aluminium surface of the stock build plate provides plenty of texture to ensure good adhesion. Adhesion is so good that some owners have difficulty removing prints. 

*Sanding is the very last resort that you should attempt, and only when you have verified that the build plate surface is not flat.*

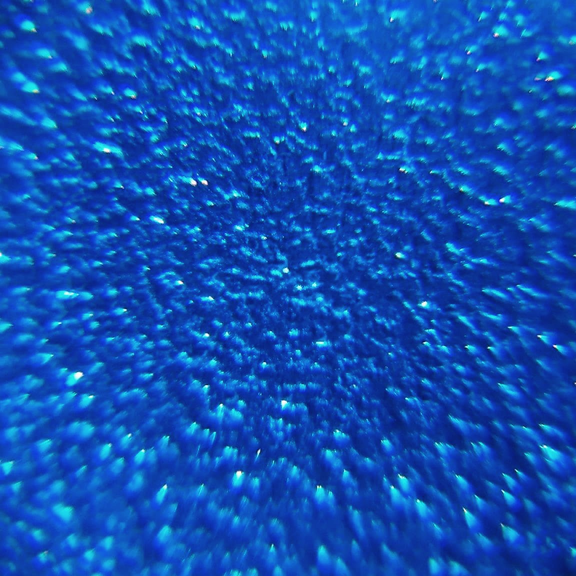
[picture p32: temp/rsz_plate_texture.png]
texture
 

### I'm using Bluecast but my prints won't stick to the build plate. 
Speciality castable resins such as Bluecast are monomer-free formulations. In this situation, the anodized surface of the build plate inhibits adhesion of the oligomers used. 

Bluecast recommends the use of a primer coat as a solution. In the Bluecast Users Group on Facebook, [a post by Bluecast](https://www.facebook.com/groups/Bluecastusers/permalink/1017917775066876/)  recommends to sand the build plate as well. Do note that raw aluminium will self anodise in time, so periodic sanding may be necessary. 

### But I've been told sanding to make the build plate surface rougher solves adhesion problems? 
That's not true at all. Once again, it is not about the texture (there's already plenty on the stock blue build plate), it's about build plate flatness and the resin formulation. If your build plate is leveled correctly and its surface is flat, and you're not using speciality monomer-free resin such as Bluecast, you will have good print adhesion. Resin will adhere even to glass as you can see in [this video](https://youtu.be/vRxkcX8kPAc) by Photocentric. 

### I'm sure my build plate is level but I still can't get a print! 
Did you just switch resins? Did you use an unsuitable resin formulated for SLA Laser or DLP printers? Are you using speciality castable resins? Did you mix the resin properly before use? Is the resin expired? Is it too cold? There are many factors that may affect print adhesion. Keep testing to find the root causes for your plate adhesion issues. 

Some resins such as Anycubic Maroon or Monocure Rapid are known to be notoriously difficult to obtain adhesion. This is due to their formulation. Try other resins, or increase bottom exposures by 10 second increments and keep testing. 

Castable and other speciality resins such as Bluecast (monomer-free) generally need longer bottom exposures and the help of a primer coat. Primers are basically just uv glue and can be found online cheaply. You can also try LOCA (Liquid Optically Clear Adhesive), 

For the vast majority of regular modelling resins, ensuring a leveled build plate and increasing bottom exposures should enable plate adhesion. Do not pay for uv glues marketed as miracle cure adhesion bonding concoctions. 

If you're positively sure it's not the resin or other factors mentioned above, and you've got your build plate leveled perfectly, and it's not warped or defective, and you still can't get a print or some parts didn't stick to the plate, [try following these steps very, very carefully.](https://github.com/Photonsters/anycubic-photon-docs/blob/master/FAQ.md#my-prints-just-wont-stick)

### I'm giving up, my prints just won't stick! 
You may have a warped or defective build plate, the plate surface may not be true and flat. Check for flatness by placing a steel rule across the build plate, against a light source, check if there are any uneven gaps showing. 

It would be more accurate to check by making an imprint. Lightly coat the build plate surface with engineer's blue dye or evenly roll a thin layer of printmaking ink. Place a sheet of paper on a known flat surface such as plate glass or polished granite /marble, then press the build plate on the paper and check the imprint for blank spots. 

### My build plate is defective and not flat, how do I fix this? 
If you've verified that the build plate surface is not flat, you can try to achieve a true flat surface by a process termed [lapping](https://www.wikipedia.org/wiki/Lapping). Unfortunately, most people will not have the tools or skills to achieve this. Try bringing your build plate to a machine shop nearby, they'll know what to do. 

If you want to try this at home, do not simply go rubbing the build plate with sandpaper, you'll probably make things worse. Proceed only if you have the necessary tools and know-how to achieve a true flat surface. 

## VAT & FEP SETUP

When you receive your new Photon, it will come with an aluminium vat frame with a FEP film already installed. Check that the film is tight by lightly tapping with your finger. If it is tensioned correctly it should sound just like a snare drum. 

Sometimes the screws may seem loose, but it may be tensioned correctly from the factory. Do not simply tighten the screws or you may then over tension the FEP. 

If tapping the FEP film does not sound correct,  it is likely loose, then simply tighten the screws till it sounds like a snare drum. 
- [Official Anycubic instructions - Youtube](https://youtu.be/Sdxf9mf7-ns) 

### How tight exactly should the FEP be tensioned? 
If it sounds like a snare drum when you lightly tap with a finger, it should be good enough. But since hearing is subjective, to be precise, you should use an audio analyser to check, factory tensioned FEP film (about 127 to 150 microns thick) is around 350Hz, but anything between 250Hz to 375Hz is fine. 

Some owners have obtained good prints with tensions as low as 150Hz, but there are also reports of leaking vats at those low tensions, For that reason, we advise 250Hz to 350Hz. Be careful when adjusting, over tensioning above 375Hz may tear your FEP film, or may cause bad prints. [(FB post)](https://www.facebook.com/groups/AnycubicPhoton/permalink/1553474471463856/)

### Why do I have to go through all this trouble to get correct FEP tension? 
When your print peels from the FEP film, there are a lot of suction forces involved. Unlike more expensive machines, the Photon does not have a tilt peel mechanism, it therefore relies on the flexibility of the FEP film to provide a clean and successful peel. 

*If the film is too tightly tensioned, your prints won't peel off properly and may stick to the build plate, too loosely tensioned and it'll have layer lines or other unwanted artifacts.* 

A correctly tensioned FEP therefore will give the best print results and avoid print failures or delamination problems. For an example of print problems which was only resolved by proper FEP tensioning, check this [FB post.](https://www.facebook.com/groups/AnycubicPhoton/permalink/1553474471463856/) 

Here is a [video](https://www.facebook.com/groups/AnycubicPhoton/permalink/1583187968492506) posted on the FB owners group showing the tremendous peel forces involved. 

### Should I coat my FEP film?
No, FEP (fluorinated ethylene propylene, invented by DuPont, sold under the brandname Teflon FEP), is already one of the most slippery materials known to science. Coating your FEP film with a hydrophobic substance like Rain-X may in fact cause bad quality prints.

### Why is my FEP film so cloudy or hazy? 
When new, the film is clear. But it is easily scratched by handling or cleaning. Use soft tissue to soak resin when cleaning up the vat, do not aggressively wipe the film as even tissue will scratch it. These micro scratches cause the film to go cloudy. Buffing the film with microfibre cloth will restore some clarity. It is important that the film is kept clear to ensure sharp and detailed prints. 

### When should I replace my FEP film? 
If you take care of it, it will not need to be replaced for months. FEP film needs to be replaced only when it becomes too scratched up or cloudy from use. If it is not replaced your print quality will deteriorate. Replace immediately if it is punctured or torn. If you notice cured resin on your LCD glass, it means the film may have a micro tear.

### How do I replace the FEP film? 
Watch the video by Anycubic for a detailed step by step. It is important to note one very important omission in that video: some replacement FEP film may come sandwiched between two layers of protective plastic. These have to be peeled off before the FEP film can be used. 
- [Official Anycubic instructions - Youtube](https://youtu.be/DLi3chV43LQ) 
- [Step by step picture tutorial - Google album](https://photos.google.com/share/AF1QipN3RLrpWpYn73-JfMIi3K09Fe8I2Nkf3PzbdlZNXSB5ElNKtLPk8Ap745EQ3rQylw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) 
- [Check FEP for protective layers - FB post](https://www.facebook.com/groups/AnycubicPhoton/permalink/1518671824944121/) (Thanks Jannick) 

### How do I test if my FEP film has protective plastic on it? 
It's difficult to see if there's protective plastic film on your FEP. An easy way to test is by dripping a few drops of resin on your FEP film, then hold the film vertical. If the resin slides downward easily without sticking and leaves the FEP clear, it's good. If the resin sticks where you dripped it and moves slowly or smears, then you have protective plastic which needs to be removed. 

### Instead of FEP film, can I use PET/PE/other film? 
Not advisable. There's a reason why FEP (Fluorinated Ethylene Propylene) is used. Besides low friction, non-reactivity, flexibility, high heat resistance, high transparency, uv resistance, etc., it is also one of the most slippery substance known to science. 

### Why do I need to use a bottle cap when replacing the FEP film? 
The bottle cap, 30mm diameter x 13mm height, will allow some slack to the film, so that when you tighten the frame down you will get approximate tension. If you don't do that, you will over tension the film and it may tear. If it didn't tear, later on you'll be wondering why all your prints fail. 

## MODEL SETUP & SETTINGS

### What settings do I need for the test (lattice cube) file? 
None. The test file that came on the included USB stick has been pre-sliced and settings configured for the 250ml bottle of translucent green sample resin. All you need to do is select the file and print. If you didn't receive this sample resin with your printer, or received a different colour sample, only then will you need to change the exposure settings. You will then need to either do an exposure test for your resin, or consult the quick settings chart (see below). 

### Where can I find the test (lattice cube) file? 
It's buried somewhere on the manufacturer's website. For your convenience, you can download a copy of the [PHOTON.photon test file here.](https://drive.google.com/file/d/1D8cWCDtwGZoMRmv6u3BkEEocH9v117yE/) 

### I just downloaded some cool .stl models from somewhere, how come it won't print? 
You first need to convert those 3D models by generating sliced layers into a format that your Photon understands and can print. This is done in what's known as a slicer program. A free slicer program comes included in the usb stick provided with your printer. 

### What other slicer programs can I use? 
If you're new to resin printing, the included slicer is best to start with. Once you've familiarised yourself with the basics, there are other slicers with more features you can try. Here is a [list of slicers](https://github.com/Photonsters/anycubic-photon-docs/blob/master/README.md#photon-slicing-software) that work with the Photon. 

### I bought x resin, what are the best settings for it? 
Every resin behaves differently, there are no best settings that will work for every resin and every machine. For a quick start, you can refer to the [community resin exposure settings.](https://docs.google.com/spreadsheets/d/1crvzMnt_8NJXAsABinoIhcOjE8l3h7s0L82Zlh1vkL8/edit#gid=0) Those settings should enable you to quickly get a print going but you will need to test and adjust from there to find the best settings applicable for your machine. 

### How do I find the optimal settings for my resin and machine? 
It used to be only possible via a messy and time consuming trial and error method involving multiple bracketed prints. But thankfully we now have the [Photon Resin Calibration Test](https://github.com/altLab/photon-resin-calibration/blob/master/README.md) aka the Photon XP Finder. This test enables you to find the optimum settings for your resin, matched to your machine, all in one simple and quick print. 

### My resin is expired, can I still use it? 
For Anycubic branded resin, first check if the date is printed in black ink. If it is, then that is the production date. For other resin brands, unless it is clearly stated, double check with the manufacturer first whether the date codes are production or best-by dates. 

Generally, most resin manufacturers advice that resin be used within one year. The dates are basically "use by" dates, not expiry per se. In practice, when kept properly in a cool dry location and unexposed to light, resin can be stored and used without issues. 

### What do the print settings mean?
This is assuming you're using the Anycubic Photon slicer program (rebadged Chitu slicer v.1.3.6) that is included on the USB stick. Other slicers may use different terminology but they're functionally the same. If you're just starting out, it's highly recommended you use the Anycubic slicer. It's basic, won't overwhelm you with bells and whistles, and just works. 

#### Bottom Exposures (Bottom layers): 
This is how long the UV light will turn on to set the layer of resin that is on your build plate for the first few layers (it's extra long to give the resin the best chance to stick to your plate and form a super hard base to help keep your part from wobbling and rocking about.) For the sample green resin at 0.05mm layers, the exposure for bottom layers is 60 seconds. 

#### Bottom layer (Bottom layers):
Simple, this one it's about how many of those super hard base layers to lay down on the base of your print usually this is 5-8 layers.

#### Normal exposures (Normal exposure time) : 
After your base layers have finished this is the time the UV will be on to cure all the rest of the layers of your print and will always be lower than your base/bottom layers setting, For the sample green resin at 0.05mm layers, the exposure for normal layers is 10 seconds. 

#### Exposure off (Off time):
Light off delay. This is the amount of time that the UV light is turned off between the end of one exposure cycle and the beginning of the next. After an exposure, the UV light turns off, the build plate lifts and peels, then descends ready for the next cycle and will wait at the bottom (resting at the set layer height over the FEP sheet, at the bottom of your vat) before the UV light comes on again for the next exposure cycle. 

Longer offtimes leave more time for the resin to settle out and form a new layer with fresh resin. This is especially useful for more viscous resins to mitigate issues of poor definition of surfaces facing the build plate

If unsure, leave the value at 1, your printer will then default to the firmware settings, usually 6.5 secs for older printers or firmware, 4.5 secs for newer printers or firmware. Any value below your printer's defaults will be ignored. The fastest prints are at default settings. 

### What is suction warping and how do I combat it, should I add a vent hole?
Vent holes are often improperly called "drain" holes, they are not for draining resin.  Imagine a glass full of water upside down in a bucket of water. When you pull the glass up out of the bucket, it stays full until the lip of the glass breaks the surface of the water in the bucket. 

In the vat, the lowest point of the print, the new layer does not (generally) rise above the level of the liquid resin in the vat. Therefore, the liquid resin inside the "bowl" or "cup" cannot evacuate, unless you add a vent hole. This is a significant cause of failures. You have to reduce the work that the stepper motor has to do to lift the platform.

Initially, In the printer vat, the inside volume of resin will be pulled up. Eventually, depending on the volume of the inside space and the volume of resin in the vat, the new layer will rise above the fluid level because the surface of the fluid will be moving down at ever increasing rates with each layer. That is, the level of the fluid inside the space and in the vat are actually moving in opposite directions. When that happens, all of the fluid inside will be released, but now you have a trapped volume of air, so you will alternate between struggling with lifting up and struggling with pushing down. 

Without vent holes, it's really a recipe for bad prints. The result is that you can get multiple failures at various heights, depending on where these extremes occur. Formlabs has a good article on [model orientation,v enting and suction cups.](https://support.formlabs.com/hc/en-us/articles/115000018124-Model-Orientation) 

### How do I hollow my model?
It depends on the software. Two popular free programs that make it easy to hollow your models are Chitubox and Meshmixer. Here is a link on [how to hollow with Meshmixer.](https://www.youtube.com/watch?v=ZXu6VYj4Um0)  

### I can see/print the supports in my .photon sliced file but not my model? 
The normals of your model are reversed. Flip them or they wont print. or your model has errors.
- [How to flip normals in meshmixer - Youtube](https://www.youtube.com/watch?v=pa9R-gPUNwg)
- [Meshmixer to repair holes - Youtube](https://youtu.be/kfmY4Wk8bhA)
- [Meshmixer top tips - Youtube](https://youtu.be/C9VDKb3W4qA)

### The slicer program says my print will take X hours, but it actually took Y hours? 
This is due to your [offtime (or light off) settings](https://github.com/Photonsters/anycubic-photon-docs/blob/master/FAQ.md#exposure-off-off-time) in the slicer. The program will calculate the print time based on the offtime value that you set, it is an estimate, it does not reflect the actual print time. To get an accurate estimate that matches your actual print time, [time your actual offtime and use that value](https://youtu.be/TWdlphFfyLY) in your slicer program. 

### Can I just use auto supports for all my models? 
No. For simple models, auto supports should generally work but as with anything automatic it will never be perfect. For a start, you can use auto supports and supplement with manual supports on parts that the software missed. But it will be best to [learn to place your supports manually](https://github.com/Photonsters/anycubic-photon-docs/blob/master/Resources/AddingSupportsForSLA3DPrinters-v1.pdf) and precisely, you will find that you will need less supports and produce better prints in the long run. 

### What angle should I use to minimize layer lines?
There isn't one best angle for printing everything. It really depends on your layer height, and the type of model you're printing. Don't forget that model orientation also plays a big part to determine the best angles. You could actually be losing details printing at the wrong angle for the layer height. 

This image by Michael Van Kesteren [from the post on the Facebook group](https://www.facebook.com/groups/AnycubicPhoton/permalink/1646527138825255/) shows the approximate best angle for each layer height to maximize details and minimize layer stepping (pixelation / aliasing) lines. 

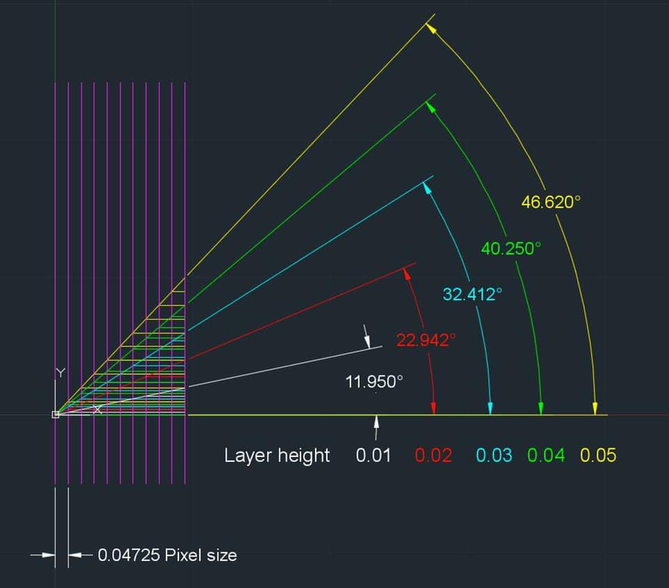
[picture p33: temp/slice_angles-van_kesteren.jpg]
angles


## PRINTING

### My first print, do I have to print the test lattice cube? 
It is highly recommended that you print it. The test file has been presliced for the included sample green resin, all you have to do is select the file and print. 

- A successful test print will confirm that your Photon works as it should, and that you have properly leveled your build plate and your FEP tension is correct. It will also confirm that your machine will reliably work as the test takes over five hours. 

- If it did not print successfully, then troubleshooting will be easier as you can rule out various other problems such as with resin, settings or slicing. 

### I'm about to start a print but the touchscreen shows a filename highlighted in red? 
That's normal, it's showing the last file you selected or printed. 

### How much resin should I pour into the vat? 
Pour resin up to the line where the chamfer starts in the vat, about a quarter up from the FEP. This is about 125ml. 

Do not exceed the line, if there is too much resin, it will rise from displacement and cause a spill. Or get into the screws and ball joint of your build plate. There have been reports that resin in the ball joint may cause the build plate to slip and shift during a print, making it out of level. Besides, once resin cures in there, it's also difficult to clean. 

### Can I add resin halfway through a print?
- Yes , no problem. You do not have to pause the print, just slowly and gently pour resin into the vat. Make sure to not bump or touch the build plate while pouring. Be mindful of displacement when adding resin. 
- Make sure to mix the fresh resin well before adding. Try to ensure the resin temperature is the same, if the difference is more than 5~10 degrees Celsius, it may cause a layer line. 

### Can I pause halfway through a print? 
- Yes, you can pause at anytime during your print. Resume as quickly as you can to ensure that your print will continue safely. However it is generally not recommended as it will most likely leave a line at the layer where you paused. 
- If you time your pause after a peel move, the chances of resuming without a line is better. 
- Do note that if you switch the printer off during a pause, you will not be able to resume. 

### Is it ok to leave resin in the vat?
Yes, as long as it's kept away from light, it's safe to leave it for long periods of time. 

### Can I leave my finished prints hanging on the build plate in the printer overnight? 
Yes, you can leave finished prints for as long as you need before removing and post processing. Just like leaving resin in the vat. 

### I hear a strange faint knock or a suction/sticking sound everytime the plate lifts. Is this normal? 
It's completely normal. It's a good sign that your print is sticking to the build plate and that the layers are releasing from the FEP film. It will be more audible during the first few bottomlayers of the print, don't worry if you can't hear it later on as it depends on the layer section being printed. 

### How do I know that my print is sticking to the build plate? 
- One easy way to tell is by listening for the sound that's made as the layer peels off the FEP. You can hear it clearly especially for the first few bottom layers. Don't worry if you can't hear it anymore later, it varies depending on the size of the layer being printed. 
- You can also use pause to check on your print, but note that you may get a line at the layer where you paused. 

### I'm printing the test lattice cube and it's wobbling? 
This is normal for the test print. The test cube is supported only by three prongs on the base, as the plate rises the print is releasing from the FEP film in a side to side flex action, hence the wobble. If your build plate is leveled correctly, the test cube will finish printing successfully. 

### My prints are not dimensionally accurate, sometimes slightly oversized by as much as 0.3mm?

First, ensure that your exposure settings are optimal for the resin used. Underexposure causes thinner parts, while overexposure will swell. Many of the basic resins swell when printed. There could also be slight shrinkage. It all depends on your settings and the brand of resin and formulations that manufacturers use. It usually isn't noticeable on organic prints. 

### I make functional parts that must fit together in a precise way, how can I achieve that? 
- After testing your resin performance, you can make the adjustments for the model itself in software. This method is not advisable as it will differ if you share the model, or use a different resin as the compensation will then be off. 
- A quick and easy way is to adjust the LCD settings in most slicer programs. 
- If the adjustments needed are slight, you can try to compensate by reducing or adding exposure times for your prints. 
- Some commercial slicing software have a "horizontal size compensation" feature that can make precise adjustments. Chitubox has also announced this feature for a future "Pro" version. 
- The Photonsters' community software, [VoxelOps](https://github.com/Photonsters/VoxelsOps) has an "erode" function that can reduce xy dimensions by precise pixels. 
- Or simply use resins that generally print true to size. Here is a [list of resins and how they fit.](https://docs.google.com/spreadsheets/d/1yDwszgncTyOxvyJho6y1kxLJquH2GsfL83KaFXT6068/edit#gid=0)

### I need to print strong parts, how do I know which resins are suitable?
There are many resins available and are formulated for various usage. Most are general printing resins suitable for models, figures, decorative and non functional prints. When deciding on resins that need to be strong, the resin must be formulated with a high degree of hardness, which also makes it brittle. Therefore, to be both strong and functional, a certain degree of flexibility needs to be blended in. For a start, check the Shore D (Shore Durometer) rating of the resin, then check the flexibility or tensile rating. A high Shore D rating over 80 combined with a high flexibility rating indicates a strong resin. 

Here is a list of some [resin strength tests.](https://docs.google.com/spreadsheets/d/1JlqLSi4sxZLdA-hHCp6Ow4isoGMNI7nlE9Nmbj1ajWk/edit#gid=0)

### My prints just won't stick? 
This is almost always a build plate leveling (tramming) issue, make sure your leveling is 100% correct before attempting these other solutions. 
- Clean the build plate carefully with IPA or other solvents. Dry before use. 
- Shake your resin in bottle well before using. Resin already in the vat may have settled and need to be stirred. 
- Preheat or warm the resin, you can use a hair dryer on most bottles to gently heat the resin to 20~30°C while swilling. 
- Preheat the build plate, same as the resin. 
- The build plate may have shifted. Try and level it again, make sure to tighten well. 
- There may be cured resin in your vat. Drain and clean. 
- Did you remember to set Z=0?
- Build plate is too high or low, this is caused by incorrectly seated ball joint screws. Disassemble, clean and retighten the build assembly. [See disassembly guide below.](https://github.com/Photonsters/anycubic-photon-docs/blob/master/FAQ.md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) 
- The FEP film may be too tight or too loose. New vats sometimes comes with loosened screws, but they could be correctly tensioned. Adjust to the [correct tension](https://github.com/Photonsters/anycubic-photon-docs/blob/master/FAQ.md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), or replace. ([FB post](https://www.facebook.com/groups/AnycubicPhoton/permalink/1553474471463856/)) ([how to tighten](https://youtu.be/Sdxf9mf7-ns)) and ([how to replace](https://youtu.be/DLi3chV43LQ)) 
- You may be using resin formulated for SLA laser or DLP printers. Try using a known resin like the sample green. Note that some resins like maroon or yellow are very difficult to work with. 
- Are you using a speciality monomer-free resin such as Bluecast? You may need a primer coat. Check manufacturer's recommendations. 
- If all else fails, check your plate level once again! 
- If you're 110% sure all the above has been tried and didn't work, your build plate may be defective. [Check that the plate surface is flat.](https://github.com/Photonsters/anycubic-photon-docs/blob/master/FAQ.md#im-giving-up-my-prints-just-wont-stick) 

### The bottom layers stick but my prints didn't form/fell off at the supports?
If your prints have good bottom adhesion but fail at the supports, this is generally due to incorrect exposure setting for your normal layers. As a first step, try increasing exposure. 
- Try increasing normal exposures by a second or two. 
- You may need to increase support tip size and depth in your slicer settings. 
- A mix of medium and heavy supports will help, and/or increase support density. 
- It can also be due to the orientation of your model. Try to angle your model and minimise large surface sections. 
- Is your model a large solid? Hollowing the model is recommended. 
- See [Model setup & settings](#model-setup--settings) above.

### I want faster prints, what is the thickest layer setting that I can slice to print with? 
The best layer slices for a good balance of speed and quality is 50um (0.05mm) thickness, but (depending on resin) some owners have sucessfully [printed at 100um (0.1mm}](https://www.facebook.com/groups/AnycubicPhoton/permalink/1582504051894231/) layer thickness. Use the [Resin Exposure Finder](https://github.com/altLab/photon-resin-calibration) from the community projects to test if your resin can print at that layer height. 

### The top of my prints are sharp and detailed, but the bottoms seem soft and less defined? 
During the printing process, resin components form covalent bonds, but layer to layer, the part remains in a semi-reacted or semi-cured state. While in this semi-reacted state, the resin retains polymerizable groups that can still form bonds across layers. Polymerization only stops when resin is fully cured via post-processing in a UV station or sunlight. 

Simply put, during printing, the layers of the model facing the FEP film are always sharply defined as the layer is exposed perfectly against it. Whereas the layers facing the build plate, previously exposed, still receive uv light from diffusion/defraction/scattering from the current exposed layer and thus will still cure slightly. This is akin to overexposure and thus details will be lost. Coupled with this, some resin always remains around the bottom parts (facing the build plate), and will also bond and cure to the details as well. 

This is a limitation of the technology but can be largely mitigated and overcome by the following:

- Ensure that exposure settings are optimal for your resin. Overexposure will magnify this issue. 
- Ensure that the model is well orientated and angled to minimise resin pooling and that important details are presented facing the FEP film. 
- Allow enough clearance for the supports so that resin does not get trapped between the bottom of the print and the build plate. 
- Set longer UV offtimes so that more viscous resins can drain during lift. It will also help to heat the resin during colder temperatures. 
- Choose resins with good light blocking formulations. Whether resins are opaque or translucent is irrelevant, the formulations determine this. 

To help in visualisation, there is a [simplified graphic explanation](https://m.facebook.com/groups/1194619320682708?view=permalink&id=1909244509220182) of this issue posted by David McGyver in the owners group on FB. 

### Resin really smells bad during printing, how do I reduce the smell? 
When you switch on your printer, you may have noticed that the little fan in the print compartment automatically turns on, and stays on. That is the number one cause of resin smells from your printer. What this fan claims to do is to draw smells into a charcoal filter below it, but in reality all it does is to circulate and distribute smells out of the print compartment and into your room. 

The simplest solution to reduce smells, without requiring complicated and time consuming additions such as in-line fans, ducting and drilling, is to simply disconnect that little fan. Here are several ways to do this: 

- Unscrew the two screws that hold the fan onto the red base plate, lift the fan, cut the red and black wires, tape and insulate the wires, and remount the now deactivated fan. 
- Open the back and bottom access panels, trace the fan's wires to the connecting block on the mainboard, and disconnect the block. 

Finally, there's also a gcode to switch the fan off, but it will be reset when firmware is updated. Search the Facebook group for fan_off.gcode if you'd like to try this. 

### Why are my prints mirrored? I checked the model in slicer and it's correct but it prints out mirrored and reversed? 
Check the LCD settings in your slicer program. There should be a tab where you can select between LCD_mirror, DLP_normal or Normal. The correct setting should be LCD_mirror. Here is a [screenshot of the selection tab](https://www.facebook.com/groups/1194619320682708?view=permalink&id=1701044800040155) for the Chitubox slicer, it should be similar in the Anycubic slicer and others. 

## CLEANING 

### How do I clean my prints? 

The recommended method is the two tub system. Fill both containers with 91% Isopropyl Alcohol (IPA) or other solvents such as 95% Ethanol. Although not necessary, heating the first tub to around 45°C helps dissolve the resin faster. 

Drop the print into the first tub and swirl for several seconds. Use a soft brush on hard to reach parts, crevices, etc. Then dunk the part in the second tub of solvent and rinse clean. Do not leave your prints soaking too long in the tubs. Remove then dry thoroughly (blow drying with compressed air works best) before uv curing. 

### What solvents should I use to clean my prints? 
Resin manufacturers universally recommend 91% Isopropyl Alcohol (IPA) or 95% Ethanol. Other solvents may be used but generally not recommended. Do not pay for overpriced cleaning solutions marketed for 3D resin printers. Here is a [solvents compatibility chart]( https://support.formlabs.com/s/article/Solvent-Compatibility?language=en_US) published by Formlabs for their resins which can be used as a general guide for most resins. 

### How long do I clean my parts in solvents? 
- For as little time as possible to get your prints cleaned of uncured resin. Do not leave your prints to soak. Some manufacturers advise no longer than 30 seconds. In a post, Formlabs mentioned that prolonged exposure to solvents may make some resins swell from absorbtion. In a related article, Ameralabs [tested prolonged soaking](https://ameralabs.com/blog/can-ipa-cause-cracks-sla-3d-prints/) of parts in IPA and found consequent shrinkage and cracking. 

### How do I clean the LCD?
You're not actually cleaning the LCD, there's a thin piece of protective tempered glass on top of the actual LCD screen. 
- Use soft tissues and a small spray of IPA to remove any dust and stains. If there is dried resin on the glass, you can carefully scrape it off with a razor. Finally, buff the glass with microfibre cloth.

### The FEP tore and there's cured resin on the LCD, how do I clean that? 
Damp a piece of cloth or tissue with IPA then lay it on the cured resin. Wait a few minutes, then with a fingernail gently try to prise the layer of cured resin off the LCD glass. If you can't easily prise it off, use a razor or glass scraper, but be careful with that. 

### How do I clean the FEP Film?
- Once you have drained the vat of resin, spray down with IPA and gently wipe off with paper towel or soft tissue. Spray again and use soft tissue to soak off the remaining residue from the FEP. You may need to repeat this several times. Finally buff the FEP with microfiber lens cloth. Be careful of dried resin on the cloth that could scratch or puncture the FEP. 

### What else can I use to clean my prints and tools from uncured resin?
- Manufacturers universally advice the use of a solvent like 91% IPA (Isopropyl Alcohol) or 95% Ethanol, Proprietary cleaning solutions or other solvents may also be used such as Mineral spirits (aka White spirits, Turpentine), etc. 
- If you have bought a water washable resin, you can simply use water and some mild soap. 
- A small brush is very helpful to get into and clean the fine grooves or details in your prints.
- Alcohol and other flamable solvents should not be used directly with ultrasonic cleaners because of the fire hazard.

### How do I dispose of saturated cleaning solvents, cleaning tools, uncured and cured resin?
- Anything containing uncured resin if no curing is possible should be disposed in a hazards facility near you. Uncured resin is considered extremely hazardous to the envoirenment and must be cured before disposal. 
- Cured resin is stable and can be disposed with the rest of the solid trash. 
- Resin saturated water (for the water washable resins) and Saturated solvents should be cured in the sun and evaporated, resulting solids can be disposed in the solids trash.
- Resin saturated cleaning paper can also be cured in the sun or in a curing UV oven and treated as solid trash.
- **Never throw resin contaminated fluids down the drain**

### Can I extend the life of my solvents?
- Yes, if you regularly cure the washing solvents along with your printed parts and filter out the solids your solvents will last longer. For methods to filter, see [this FB post.](https://www.facebook.com/permalink.php?story_fbid=10158197292218680&id=651553679) about it 

### How long can I keep the resin in the vat?
It depends on environmental factors and type/brand of resin, typically if the resin is kept out of light and moisture/dirt it may sit in the vat for a few weeks. Clear resins tend to sit better, opaque resins will need more stirring before use to mix the pigments back. 
- Check for loose cured resin or stuck resin, you will need to clean that out. 
- Cover the vat, you can cut a piece of cardboard that fits over the vat, or print one out on an FDM printer. Here is a good vat cover [found on Thingiverse.]( https://www.thingiverse.com/thing:2837171)
- Before printing, carefully stir the resin for 1 - 2 minutes with the plastic spatula, be careful not to scratch the FEP screen.
- Do not leave the build plate hanging with uncured resin, take it out and clean with IPA, leave it out until you are ready to print, this will lessen the weight on the single lead screw thus prevent deformation and potential Z wobble. 

### Can I put excess resin that doesn't get used in a print back into the original bottle?
- Yes, but you should strain out any debris first using a filter.
- You can keep the used resin in medicine bottles separately. 

### Water washable resin, how to dispose of the dirty water after washing the print? Wash it down the drain? 
**Do not pour it down the drain!** 

Water washable resin works because it uses water soluble monomers. Water isn't an acrylate. Water can not cure. When you dilute resin into anything that's not capable of curing, it won't be inert again. 

Even after you expose the mixture to UV, the photoinitiators in the diluted resin water will still cleave and generate free radicals. If some acrylate molecules are nearby there will be a tiny bit of chain growth taking place. The spent photoinitiators, pigments, and the portion of the resin that actually cures will settle out, but the rest will still remain diluted in the water. 

*What this means is that resin cannot cure to completion in solution (water). It cannot cure due to change in concentration of reactants and there will be contaminates in the wash that are not safe down the drain.* 

The only proper way to dispose of the wash is to reduce solution by evaporation, and then collect and UV cure the resin residuals and dispose of them properly. 

[Original discussion pertaining to Water Washable resin disposal safety on the Facebook Group.](https://www.facebook.com/groups/AnycubicPhoton/permalink/1866245396853427/)

## POST PROCESSING

### My print stuck so well to the build plate that I can't remove it? 
Congratulations on having a well leveled plate. Sometimes prints adhere so well that removal is difficult. Try the following methods to remove recalcitrant prints, in order of recommendation:

- Heat up the print and build plate to around 40~50°C by using a hair dryer or running them under hot water. Your print can then be easily removed. 
- Freeze the print and build plate for a couple of minutes, a light tap and it'll pop off. 
- Use a razor to lift a corner, push a spatula under the lifted edge and remove. 

### How long should I cure my print?
The best way to find out if your print has cured enough with sunlight or a UV light set up is to find an area where you don't mind a mark and try to dent it with your fingernail, If you can then it's not ready yet, and as soon as you can't dent it it's ready. Do not overcure as resin may become overly brittle, and white or clear resin will turn yellow. 

### Should I remove supports before or after curing? 
It depends. While it is easier to remove before uv curing (it's softer and you can just pull or rub them off), you may want to remove them after, especially thin parts that may warp during the curing process. 

### How durable are the prints? Will they break if I drop them? 
It depends on the resin used. Unlike PLA or ABS, regular hobby grade resin prints are quite brittle and can easily break when dropped. There are specially formulated resins for prototyping or even functional usage which have different properties such as flexibility, hardness and uv resistance. Once you have familiarised yourself with your printer using the sample green resin, you might want to experiment further with different resins. 

### Why do I get white chalky residue on my prints after curing? 
The white residue appears if there's moisture or water on your prints when you UV cure. One way to avoid this is not to wash your prints in water after cleaning in solvents. Always make sure your prints are completely dry before final UV curing. 

## TROUBLESHOOTING

### Why does my build plate move / slip during a print? 
Make absolutely sure that you have tightened the grub screw that secures the build plate fully. This can also happen if there's another grub screw already in the hole preventing tightening fully. Also check that the screws in the carriage arm of your build plate (there are three of them in there) are not loose. Or, if you had overfilled the vat and resin has gotten inside, it makes the grip of the ball joint slip. You'll need to disassemble the build plate assembly and clean thoroughly with IPA then. 

- [Official Anycubic instructions - Youtube](https://www.youtube.com/watch?v=VdiNI_Xu6bI)
- [Photonsters Video Instructions - Youtube](https://www.youtube.com/watch?v=Uc8senzACFM)

First remove the 4 bolts you can see just either side of the carriage arm (with the red platen knob on it) put them some place safe then take the build plate off, you will see three more screws, unscrew these and then you can take the mechanism of the ball joint apart, be sure to note where it all goes so you can easily put it back together again. 

Now you have it all apart, clean everything with IPA and remove any cured or uncured resin you find, Then just put it all back together nice and tight and relevel the build plate. 

### My printer stopped and the message on the touchscreen says my print is finished but it's not? 
Did you replace the USB stick with a known good branded one yet? The included USB stick is known to be problematic and causes issues like this. 

### My Photon doesn't work anymore, the touchscreen is fine but the Z motor stopped working, the fans are off, and the LCD doesn't show anything. Is my printer dead? 
If you had accidently switched the printer off in the middle of an operation, or if there was a power disruption, it may cause a corruption to the EEPROM. The printer can be easily revived by resetting the EEPROM by reflashing the.gcode file. [Download the factory defaults](https://github.com/Photonsters/anycubic-photon-docs/blob/master/firmware/factory-defaults.zip), extract the .gcode file, put it on your usb stick and 'print' the file. 

### My printer randomly resets during printing / I have another problem not listed in this FAQ? 
- Most of the known problems are listed and there are a few solutions to test. See the [KNOWN ISSUES SECTION.](https://github.com/Photonsters/anycubic-photon-docs/blob/master/known-issues/photon-known-issues.md)

## MAINTENANCE

### What maintenance do I need to do to keep my Photon running well? 
Nothing much really. Keep everything clean by wiping down with a microfibre cloth slightly dampened with IPA. Wipe resin drops and spills off immediately with IPA and tissue. Keep your vat and FEP clean. Keep the LCD screen perfectly clean. Dust off and keep the printing compartment clean. And every three months or earlier, depending on usage frequency, clean and replace the grease for the lead screw. If it squeaks, do this immediately. 

### What grease should I use for the lead screw (Z rod)?
Viscous grease. The thick, creamy, toothpaste consistency type.
Aka machine grease, cosmoline, gel grease, gear grease, etc. 
White Lithium grease is well received. You could also try "non flick" motorcycle chain grease. 
Just make sure the lubricant is not thin and runny. Do NOT use WD-40!

### How do I replace the grease on the lead screw? 
Wipe all the old dirty grey grease off with a cloth rag, or kitchen towels. Then really get it clean by wiping again with solvent and use a toothbrush to get between the threads. IPA works great. Make sure solvent doesn't drip down into the stepper motor beneath. When it's clean and dry, regrease with good quality grease, apply by dabbing onto the entire length of the screw, then switch on the printer and run the slide block up and down. 

### Why do people apply Kapton tape all round the perimeter of the LCD glass screen? 
Although not strictly necessary, most owners apply tape as an added safety measure in case of resin leaks or the LCD being pulled off together with the vat. 
This post [explains why](https://m.facebook.com/groups/1194619320682708?view=permalink&id=1482113671933270) in more detail. 

## WARRANTY 

### My Photon broke down, is there a warranty? 
According to the warranty terms stated on Anycubic's website, the [standard warranty period](http://www.anycubic3d.com/maintenance_policy.html) is three months for the LCD mask panel and UV LED unit. All other components (except tools and FEP film) are warranted for twelve months. 

## ACKNOWLEDGMENTS

### Where did all this information come from? 
Most of the information, insights, tips and tricks were gleaned from posts by the helpful members of the [Anycubic Photon Printer Owners Group](https://www.facebook.com/groups/1194619320682708), tested, verified and curated by the Photonsters team. Special thanks goes out to Flint Read for his invaluable "Photon Guide & Tips" from which formed the initial core of this FAQ.

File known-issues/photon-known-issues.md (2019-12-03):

**CONTACT ANYCUBIC SUPPORT FIRST!** 

This should be your first point of contact for faulty machines, some of the fixes here may void your warranty, proceed at your own risk! ([Anycubic Support Contact Page](http://support.anycubic3d.com/submit.html)) 

The following issues and solutions have been compiled from cases reported by Photonsters in the [Anycubic Photon Printer Owners Group](https://www.facebook.com/groups/1194619320682708) on Facebook. 

**IMPORTANT NOTE!**

As of September 2019, Anycubic has been shipping printers which deceptively look like Photon printers but are not. These new printers are incompatible with the original Photon printers. The troubleshooting guides and fixes provided here do not apply to this new printer. 

---

## KNOWN ISSUES

- Filenames on USB stick must not contain special characters as the Photon will not read them. Try also to avoid long filenames although they have been confirmed to be fine. [(FB post)](https://www.facebook.com/groups/AnycubicPhoton/permalink/1370647173079921/)
- Faulty internal USB cable. (loose or bad connection, causing random resets)
- Random resets possibly caused by internal memory buffer issue. 
- Z-wobble. 
- Included USB stick is faulty. (replace with known good usb formatted FAT32) 
- Bad PSU brick. (included with older Photons before yellow windows)
- Random resets / reboots. 
- Random freezes mid-print. (usually usb related)
- LCD half screen issues. 
- LCD screen flickering during print or corrupted and shifted layers or artifacts. [(FB post1)](https://www.facebook.com/groups/AnycubicPhoton/permalink/1322462231231749/) [(FB post2)](https://www.facebook.com/groups/AnycubicPhoton/permalink/1379338082210830/) [(FB post3)](https://www.facebook.com/groups/AnycubicPhoton/permalink/1539849456159691/)) 
- Screen cable broken / sheared during shipping. 
- Mainboard failure. ([see how to test video](https://youtu.be/F69UMKYKvbY)) 
- Memory errors. 
- Dead motor / Z axis. ([FB post](https://www.facebook.com/groups/AnycubicPhoton/permalink/1540155946129042/)) 
- Failure to set homing offset values. (config.gcode issue, reflash config.gcode)
- Layers shifting/shearing on LCD during print. (occurs on certain files, firmware issue, downgrade to v4.0.11 to fix)
- Loose print bed head / print head too short. (build plate assembly issue)
- Slicer does not display STL. (PC graphics board driver issue)
- Slicer up to 1.3.6 has a floating point bug in layer sizes other than 50u making layer height float. ([FB post](https://www.facebook.com/groups/AnycubicPhoton/permalink/1398780826933222/))
- Z motor stops moving mid-print, LCD keeps exposing resin, no error message, stopping print and moving Z via menu works.
- LCD screen light bleed. UV test rectangle shows dimly, low contrast, entire screen letting UV through slightly. Possibly fpga/contrast issue reported fixable by firmware update. [(FB post)](https://www.facebook.com/groups/AnycubicPhoton/permalink/1531910403620263/)
- LCD stops displaying layer slices halfway through a print, all other functions still continues. [(FB post)](https://www.facebook.com/groups/AnycubicPhoton/permalink/1548763945268242/) 
[(Youtube video)](https://youtu.be/S-G0X7rQl8w) 
- Squares print rhomboid, circles are skewed. 
- Build Plate Does Not Reach Z0 Bottom. 

---

### *.photon files can't be detected or won't print on Photon printer. 
#### Symptoms
- *.photon sliced file prepared in anycubic/chitu slicer v1.3.6 or Chitubox is not detected or won't print on an original Photon printer. 

#### Suggested Fixes
- Check firmware version of printer, if it shows v3.4.x then it is **not** an original Photon. You have a new Photon, otherwise known as a Fauxton. These are new printers that look like an original Photon but the motherboard and firmware has been changed. 
- Try to reslice your model and obtain *.pws output files. These are the only files that will print on a Fauxton. 
- If you have been sold one of these new printers without your knowing, you may try to seek resolution from your Seller. 

### Random Resets / Memory Errors / USB Read Problems
#### Symptoms
- Printing freezes at random points, resets to homescreen.
- Random freezes with error code. (see error codes below) 
- File browser not displaying any models. 
- USB key light indicator is off, but plugged in (it should always be on.)
- If you wiggle the USB key, you can read files again. 

#### Suggested Fixes
- Replace stock USB key with a known good branded one, formatted to FAT32. 
- Only have one file on USB, using short name and no non english characters or spaces.
- If problem still occurs you might have defective USB extension cable or faulty mainboard.
- Video instructions for checking USB cable [Youtube video](https://www.youtube.com/watch?v=6JowsfJEdHs) 
- Test with a new USB Extension cable. this is male to female type, you can easily access this by removing the four screws holding the rear vent panel. UNPLUG POWER BEFORE DOING THIS! 
 Unplug the male connector to the mainboard and plug in a replacement, then plug in your USB key. If this fixes the problem, contact Anycubic for a replacement cable as it uses a special external mount.
- If you have a small USB key, you can plug it directly to the mainboard for testing, (Not recommended as a permanent solution.)
- If the problem isn't solved with replacement USB cable, then you might have a faulty mainboard. Contact Anycubic immediately for a replacement or new machine. Firmware updates will not solve the USB issue.
- Before printing try to remove power cable with no USB plugged in, wait for 1 min then plug power and USB back in. Possible cause might be IC Memory buffer issue, unplugging the power should reset it. (Update 15-07-18) 
- Check printer driver reference voltage is between 1.07V to 1.16V. If not, tune it to around those figures. [FB post](https://www.facebook.com/groups/AnycubicPhoton/permalink/1404990436312261/) (confirmed by Laszlo Cook.)
- Check power supply unit (PSU) version. Early versions are known to be faulty. Replace with another 12V 6A unit. [Comparison photo](https://raw.githubusercontent.com/Photonsters/anycubic-photon-docs/master/known-issues/photon_psu_comparison.png)

### Slicer Won't Display Model / Does Not Work
The Anycubic Photon Slicer currently does not support intergrated graphics driver, or resolutions above 2K.

### Loose Build Plate / Plate Too High
#### Symptoms
- The build plate easily tilts side to side even when grub/mount screw is tightened,
- The build plate sits too high from the FEP and cannot lower any further.
[Photo of the print bed assembly here](https://github.com/Photonsters/anycubic-photon-docs/blob/master/known-issues/photon_bed_mount_assembly.jpg) 

#### Suggested Fixes
- Disassemble build plate assembly, clean and reseat ball joint. [Youtube video](https://www.youtube.com/watch?v=VdiNI_Xu6bI) 
- Check your build plate mount screws. [Youtube video](https://www.youtube.com/watch?v=Uc8senzACFM) 
- Remove the grub screw. 
- Remove the four screws holding the build plate. 
- Tighten three more screws inside that help secure the ball joint.
- Make sure to clean out any resin with IPA or other solvents. 
- All screws should be tight.
- Realign and adjust the build plate. 
- If you can't tighten down the build plate with the grub screw, make sure there isn't two screws in there. 

### Z Wobble / Non Random Layer Artifacts 
#### Symptoms
- Non random layer artifacts visible on surfaces no matter what orientation of print. 
- Consistent banding lines approximately 2mm apart. 
- Consistent warped prints. 

#### Causes and Suggested Fixes
 - First, try cleaning the lead screw (Z rod) and reapply with good quality viscous grease. 
 - FEP film may be loose. Tighten the FEP. [Youtube video](https://youtu.be/Sdxf9mf7-ns) 
 - Replace the FEP film. [Youtube video](https://youtu.be/DLi3chV43LQ) 
 - Tighten the eccentric roller of the slide block. [Anycubic official video](https://www.youtube.com/watch?v=4cfCWmHtsy8) 
 - Brass nut of the lead screw loose or not seated properly. Remove, clean, reseat and tighten the four screws. 
 - Bent or warped motor dampener /cushion. Open back vent hatch, check and replace if necessary. 
 - Motor mounting causing lead screw to be off centre or not perpendicular to lcd glass. Tighten the two screws that hold the motor. Sometimes, loosening the two screws slightly may provide a [temporary fix.](https://www.facebook.com/groups/AnycubicPhoton/permalink/1547616112049692/) 
 - Replace entire integrated motor lead screw assembly.  
 
 ### Layer Shifting / Shearing On LCD During Print 
 #### Symptoms
 - Only occurs on certain prints, depending on placement and/or geometry. 
 - Prints look like they have been sliced / cut and moved onto another part of the build plate. 
 - Layer images on LCD look sheared and do not correspond to layer images showing correctly on touchscreen. 
 - Checking the Photon file reveals no problems. (in slicer or Validator) 
 
 #### Causes And Suggested Fixes
 - Firmware bug affecting all firmware except v4.0.11 (Fixed in 4.2.18+)
 - Do a 'dry run' and use timelapse camera to check if the LCD images shift or shears during print.
 - Suggested fix is to upgrade firmware to 4.2.18+ [FB Post](https://www.facebook.com/groups/AnycubicPhoton/permalink/1644853745659261/)
 
  ### Anycubic Photon Slicer Does Not Display STL
  - Update display driver.
  
  ### Anycubic Photon Slicer Does Not Run
  - Reinstall slicer program.
  - Reinstall C++ distribution library. 
  https://support.microsoft.com/en-au/help/2977003/the-latest-supported-visual-c-downloads
 
 ### LCD Displays Only Half Screen
 #### Symptoms
 - LCD displays half the screen only, touchscreen display shows correctly. (This not related to flickering LCD issue) 
 
  #### Causes and Suggested Fixes
  - Check that all cable connections are seated correctly. 
  - Contact Anycubic Support. 
  - Update or reflash firmware obtained from Anycubic website. 
  
 ### Squares Print Rhomboid, Circles Are Skewed
 #### Symptoms
 - A cube when printed turns out to be not perfectly squared. Cylinders when printed have a lean. [FB post](https://www.facebook.com/groups/AnycubicPhoton/permalink/1571701802974456/) 
 
 #### Causes and Suggested Fixes
 - Check that the rail column is perpendicular to the red base plate. It may be a small degree off, and could be leaning forward or to the sides, or a combination. Use a small engineer's square to check accurately. If the column is leaning it will cause prints to skew. Adjust the 4 mounting bolts for the column, you may have to loosen and tighten so that the column is perfectly vertical. It takes some trial and error to get it right. If not, you will have to shim the column base. [FB post](https://www.facebook.com/groups/1194619320682708?view=permalink&id=1479801292164508) 
 
### Build Plate Does Not Reach Z0 Bottom
#### Symptoms
- After leveling and setting Z=0 correctly, prints still fail. [FB post](https://www.facebook.com/groups/AnycubicPhoton/permalink/1502900896521214/) 

#### Causes and Suggested Fix
- Check if the carriage arm is hitting the top of the vat wall and is thus prevented from reaching Z0 to the bottom of the vat. 
- A simple fix is to add 4 washers as spacers to the 4 screws that secure the build plate to the ball joint assembly. 
 
### Unresponsive Z Carriage, LCD Inactive, Dead Fans. 
#### Symptoms
- On boot, Z carriage does not move, touchscreen Z controls are unresponsive. LCD test shows nothing on screen, fans are dead. 

#### Causes and Suggested Fix
- Bad shutdown, or power interruption, no matter how slight sometimes causes corruption to the EEPROM. 
- Download the factory defaults gcode file and reflash EEPROM. 
- Or update the firmware. 

 ### Other Random Issues
 #### Symptoms
 - After you have tried all the fixes above, machine is still behaving abnormally. Possibly faulty Mainboard.
 
  #### Causes and Suggested Fixes
 - Check for mainboard faults using mulitmeter following this video. [Anycubic Official Video](https://youtu.be/F69UMKYKvbY) 
 - Replace Mainboard.
 
## Error Codes
These are some of the known error codes that the Photon will display. 

#### M_10000
[FB post](https://www.facebook.com/photo.php?fbid=2212662805488791&set=gm.1625910550886914&type=3&permPage=1)

#### M_11820
Machine will randomly freeze during print and display error, Z does not retract, fan stays on.

#### M_11800
From Anycubic engineer, "this means USB is not plugged in". [Troubleshooting and fixes for M_11800 Error.](https://github.com/Photonsters/anycubic-photon-docs/blob/master/known-issues/M_11800-troubleshooting-and-fix.md) 

#### M_11000
USB read problem, Replace with new good branded USB stick, formatted FAT32.

#### M_400
USB cable problems? [FB](https://www.facebook.com/photo.php?fbid=2276138085762970&set=p.2276138085762970&type=3&permPage=1)

#### T_100
"No TE signal for 2K LCD" 
This indicates an LCD screen physical connection problem. 
[YoutubeVideo](https://www.youtube.com/watch?v=b4NgkbUrcwc&t=302s) 

The Tearing Effect Signal (TE) is a feedback signal from the LCD Controller to MCU. This signal reveals the display status of the LCD controller. In the non-display period, the TE signal will go high. Therefore, this signal enables the MCU to send data by observing the non-display period to avoid tearing. 

According to hardware Master César Fernández, once a bad LCD or bad LCD connector is ruled out, next things to look for in order of economy are:
- Reinstall firmware for a version very different than the current one and test. 
- Check Onboard LCD connector, replace if damaged and test. 
- Check R15, R16, R24 Resistors and Q10 transistor, replace if shorted or wrong value and test. 

If none of the above work, then:
- Replace Mipi bridge ICs and test. 
- Replace FPGA and test. 

[Diagnostic Method - FB](https://www.facebook.com/groups/AnycubicPhoton/permalink/1700449923432976/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)

#### T_88
Meaning: "2K LCD signal errors (TWICE)"; Reconnect the cable of the 2k screen is ok.
[FB post 1](https://www.facebook.com/groups/AnycubicPhoton/permalink/1373149382829700/) [FB post 2](https://www.facebook.com/groups/AnycubicPhoton/permalink/1603268679817768/)

### Complete list of onscreen error codes
[Complete list of onscreen error codes, probable causes and solutions](https://github.com/Photonsters/anycubic-photon-docs/blob/master/known-issues/LCD%20errors%20shown%20on%20Photon%20screen%20and%20solutions.xlsx) as provided by Anycubic.

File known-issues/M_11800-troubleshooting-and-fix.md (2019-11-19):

## M_11800 Memory Error
### Troubleshooting and Fixes
According to Anycubic, the M_11800 error means that "the USB stick is not plugged in". Removing and replugging the USB stick will often fix the problem if it wasn't plugged in fully or seated properly.

But more often than not, it is a devilishly difficult problem to diagnose if it is something else that is making your printer *think* that the USB stick is not plugged in. 

Try these steps one by one ;

- First, remove usb stick and try a power cycle. Switch off, unplug from mains, wait 10 mins, restart. Wait 1 min, plug in usb stick, wait a while before browsing files on the usb. 

- If not, try a few other usb sticks. Beware of fakes, try good known brands, formated FAT32. 

- If not, open back panel, unplug usb extension cable from mainboard, plug good mini usb stick directly. 

- If not, try a firmware update. Be sure to print all the update files in the given sequence.  

- If not, try another PSU. 12V 6A or higher amps. Possibly power issues causing udisk unmount. 

- If not, there's nothing else you can do unless you're willing to open it up and dive into troubleshooting cold solder joints, C10 filter capacitor, or driver voltage, etc. 

If the above didn't fix the problem, then you'll have to contact your vendor or Anycubic Support. It is most likely a mainboard issue.

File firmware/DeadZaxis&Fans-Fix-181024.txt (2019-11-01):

# Dead Z axis fix by anycubic

Original FB post: https://www.facebook.com/groups/AnycubicPhoton/permalink/1479964245481546/

**Kudos: Curtis Miller**

I got these files from Anycubic support to fix the issue where there's no movement on the z-axis, the fans don't turn on, and no UV light on the screen. They provided the following instructions and an image which contradicts them:  

----

The attachment firmware for your reference  

The refresh order is: 

- fpga26 
- 导出状态文件.txt
- 机器参数.gcode

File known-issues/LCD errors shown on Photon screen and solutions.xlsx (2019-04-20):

Error types | Error code | Possible causes | Solution
USB error | M_3e | bad contact | re-insert the USB stick
 | M_800 | USB timeout error | re-insert the USB stick
 | M_1000 | cannot find memory | re-insert the USB stick
 | M_2000 | parameters error | re-configure parameters
 | M_8000 | read and write errors of USB | update firmware or change for a new USB
 | M_10000 | feedback errors | re-insert the USB stick and printing
Memory error | M_11800 | timeout errors when read memory | re-insert the USB stick and printing
 | T_08 | 2K LCD signal errors | reboot the mainbaord
 | T_40 | watchdog timeout | reboot the printer
signal errors | T_80 | 2K LCD signal errors (TWICE) | reboot the mainboard or re-adjust the wiring connector of the 2k LCD screen to mainboard
 | T_100 | NO TE signal for 2K LCD | reboot the mainboard or re-adjust the wiring connector of the 2k LCD screen to mainboard
 | T_88 | 2K LCD signal errors (TWICE) | reboot the mainboard or re-adjust the wiring connector of the 2k LCD screen to mainboard

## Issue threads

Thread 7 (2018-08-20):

Consider splitting up the "cool models for testing" section

moppius, 2018-08-20:
It would probably be more useful to split the Readme's "cool models for testing" section into two sections:
### 1. **Calibration Models**
This section would just have one or two standard calibration models that everyone tends to use for testing, and the second section would contain a list of links to sites like Thingiverse, CGTrader, TurboSquid and any other repositories of free or paid 3D-printable models.

### 2. Model Repositories
This would probably be of more general use than the current list which is a mix of calibration models, standard test pieces and just random other sculpts.

Everyone has a different definition of "cool" anyway 😄

moppius, 2018-08-20:
I'm quite happy to do this on my fork and submit a PR for the changes.

X3msnake, 2018-08-21:
i can add you to the photonsters team and u can do it directly on the
project repo.

No dia segunda-feira, 20 de agosto de 2018, Paul Greveson <
notifications@github.com> escreveu:

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

--
Com os melhores cumprimentos,
Vinicius Silva

X3msnake, 2018-09-10:
sent u an invite to the team

Closed 2018-10-11.

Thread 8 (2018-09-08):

Safety of Resins

NardJ, 2018-09-08:
I just sent the following question to MonoCure about the safety of their resin. The answer will be input for the safety page.

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

X3msnake, 2018-09-08:
ok

No dia sábado, 8 de setembro de 2018, Nard Janssens <
notifications@github.com> escreveu:

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

--
Com os melhores cumprimentos,
Vinicius Silva

NardJ, 2018-09-09:
So I got this back:
> We have been developing and manufacturing UV products for over 30 years! One of my Chemists has been with us the whole time. His health has not been affected by any of these chemicals. I have never seen him wear a mask or gloves! If our resin had any dangerous levels of VOC emission then the SDS would state that as a respiratory warning. It sounds like you are doing everything in the way of protection so all will be fine.

webbyeasy, 2018-09-09:
Thats what was said to me when I asked about it lol. But, Australian health
compliances are very strict, so I do trust the information in the SDS. But
in saying that SDS generally only applies to the product in its packaged
state and NOT by products of a reaction such as UV exposure. Just take the
necessary precautions such as active venting and making sure you dont cross
contaminate resin into the house.

On Mon, Sep 10, 2018 at 12:41 AM, Nard Janssens <notifications@github.com>
wrote:

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

NardJ, 2018-09-09:
Yeah the SDS  has some interesting snippets. I asked a follow up question. Curious what they will answer:

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

webbyeasy, 2018-09-10:
its a good article, but why single out Monocure? I would be far more
concerned of resins manufactured in countries with far less material safety
laws then Australia.

I would put links to the SDS of most UV Resins in the article first and put
a caveat in if you plan to write only about Monocure. or just remove a
direct reference to Monocure and make the article fair and objective.

I know you are been objective, but reading it for the first time felt like
you are singling out Monocure. Lets not do that on our public docs.

When I've been writing the Phontonsters documentation Ive avoided referring
to particular products and company.

Also if you plan to quote Monocure in the docs from your email
correspondence, please make sure you have permission from them to do so
first.

PS: I use a painters mask

On Mon, Sep 10, 2018 at 3:19 AM, Nard Janssens <notifications@github.com>
wrote:

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

X3msnake, 2018-09-10:
A good guy to talk about the resins is Stefan Guiducci on the Anycubic
photon Group

Nard Janssens <notifications@github.com> escreveu no dia segunda,
10/09/2018 à(s) 14:58:

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

--
Com os melhores cumprimentos,
Vinicius Silva

jdlizard, 2019-01-18:
I think you can't totally trust a sds sheet to keep you safe. Research is limited right now on the resins and being over protective will never be a bad idea.  I work with these resins at work and we use vacuum hoods.  Not all of our resin printers are hooked to ventilation but all post processing is done under a hood. We do not wear respirators but we also never smell resin under the hood.

zeelobby, 2019-04-11:
Let's be honest. Their response is pretty indicative of how SDS are handled. It's basically a legal catch-all in case something happens. Better to put more and not worry when respiratory problems pop up 10 years from now. "Well we said watch out for vapors".

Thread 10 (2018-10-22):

IWantToHelp

bartwaw, 2018-10-22:
Hi,
here's more detailed description of chitu gcode settings - get them from Orbeat D100 distributor.
As i can see, D100 is using same board as Photon.
I've also connected external stepper driver - TMC2208. On board there are exposed soldering points for connecting external drivers.
Now i'ts silent - i suppose that on board is A4988.

Got also question - photon file editor.
can you make few improvements:
1. better file opening - that open dialog is annoying - is possible to make something similar to windows open dialog ?
2. can you add file types .cbddlp

cheers
bartek

heres what i've got from distributor.
Hope it helps

-------------------------
;[[After the semicolon is a comment, please modify the corresponding parameters according to the comment, the command after the semicolon will be ignored]]
The basic format is Mxxx Ixxx, Mxxx Txxx or Mxxx Sxxx, where Ixx (which is the letter I, the first letter of the integer, not the number 1) followed by an integer, which can be either decimal or hexadecimal (starting with 0x) ), followed by Sxx is a floating point number

;

M8513

[Stepper motor direction control] The direction of I1 and I-1 is just the opposite, so if the motor direction is wrong, either change the wiring or change the direction parameter.
M8002 I-1; X stepper motor direction, I1 or I-1
M8003 I1 ; Y stepper motor direction
M8004 I-1 ; Z stepper motor direction

;[XYZ axis extrusion head/platform movement configuration] only affects the actual movement direction of the manual interface button;;;;;;;;;;;;;;;;;;;;;;;;;;
M8005 Z0 ; 0: Z-axis direction, forming bracket movement,
; 1: Z-axis direction resin groove movement

;
; [Speed / Acceleration Settings] Speed in mm / s, acceleration in mm / s ^ 2
M8006 I40; the maximum starting speed, when the speed of movement has passed this speed, it will start at this speed.
This speed is mainly to prevent out of step, this value is too small, will cause the rail angle bump when rounding
M8007 I25; the maximum rail bending speed value (corresponding to the jerk speed in the open source firmware), if the actual rail bending speed of the motion is greater than this value,
; will force the movement to slow down. When filling, there will be a lot of reciprocating motions, this value is large, the noise is large, and it is easy to lose steps.
; This value is small, slow, and print quality is relatively poor when printing speed is high
M8008 I1000; Acceleration, the larger the value, the larger the average speed of actual operation, but the noise is also large, the value is small, and the actual speed will be smaller.
;
;[[[step related parameters]]] After the parameters are set, please print a cube, then measure the size with a ruler to confirm that there is no problem with the parameters.
;
M8009 S0.0125; [XY value of each step of XY] is 20 teeth, the pitch is 2mm (mxl specification, 2gt is 2mm), 1.8 degree stepping motor,
; 16 subdivision, then (20 * 2) / ((360 / 1.8) * 16)
;M8009 X0.0125 Y0.0125 ; If you need to set the X, Y stepper motor parameters independently, you can use this command
;
M8010 S0.000625 ; [Z mm value per step] On a non-delta machine, calculate the formula: lead / ((360 / 1.8) * 16).

;
;[Various speeds maximum] In order to ensure the machine can be stable, please set according to the measured results.
M8012 I200; maximum speed of XY motion mm/s
M8013 I5 ; maximum speed of Z motion mm/s

;
;[zero speed]
M8015 I10 ; The first zero return speed when Z is zero, the speed is faster, the Z movement speed of the manual interface is also the same as this speed, and the Z axis is also used for this speed.
M8015 S30; Zero return speed when XY is zero, the speed is faster, the XY moving speed of the manual interface is also the speed of the XY axis shifting
M8016 I6 ; The second zero return speed when Z returns to zero, the speed is slower. Decreasing the second zero return speed can improve the repeat positioning accuracy of the limit. If the parameter is 0, the second zero is not performed.

[Z-axis demoulding rise and fall speed] During the demoulding process, first slowly rise, then rise quickly, then quickly fall
M8015 T2 ; Z-axis slow release rate
M8016 T6; Z-axis demoulding rapid rise and fall speed
;

; [When the Z axis is demolded, the dwell time after the rise]
M8016 D0; the unit is ms (milliseconds),
;
; [X, Y, Z maximum stroke] unit is mm
M8024 I0 ; X maximum stroke, the shaft is used for demoulding in the X direction or used as a scraping material. If the direction does not require movement, the stroke is zero, and the manual interface cannot operate the scraping. If non-zero is set, the shaft is turned on. The axis will be zeroed
M8025 I0 ; Y maximum stroke, this axis is used to block the lens of the projector. The signal is blocked at the position of zero return. It is not blocked at the maximum stroke position. If the axis movement is not required, set the parameter to 0, manual interface. Also unable to operate, if non-zero is set, the axis will be reset to zero
M8026 I150 ; Z maximum stroke, the stroke is the movement stroke of Z, be sure to use the ruler to measure it, carefully set, pause and print, the Z axis will stay at the maximum stroke position
;

;
;[XY axis limit switch position type]

M8029 I0 ;0: One-sided limit, only use X-, Y-, Z-limit, do not use Z+
2: Bilateral limit, if Z+ and Z- limit are used at the same time, Z+ can limit the maximum stroke of Z

;
;
;
;[XYZ limit switch wiring type] If this configuration is wrong, the motor will not move and the buzzer will be in a certain direction when the motor is operated by the manual interface.
; will make a drop of sound.
Simple judgment method, if the configuration is normal, when the limit is changed to the limit, the buzzer will make a drip sound.
When the limit is changed to the unrestricted position, the buzzer will not sound. If the opposite is found, modify this configuration.
M8029 T0 ;0: Limit switch normally open (when unrestricted - and s voltage is high level, low level when limit)
; 1: Limit switch normally closed (when unrestricted - and s voltage is low level, high level when limit)
;
;ˇľZ-axis limit switch positionˇż
M8029 S0 ; 0: The limit of the extrusion head closest to the platform, the limit is connected to Z-
; 1: the limit of the extrusion head is farthest from the platform, the limit is connected to Z+
;
;[Whether the XYZ axis returns to (0,0,0) after homing,]
M8029 C0 ; 0 : return to the XYZ (0,0,0) position, that is, the position where the extrusion head returns to the coordinate zero position
; ;1 : Stay in the limit position
;
;;

;ˇľFan 1 controlˇż
M8030 I-2 ;>0: If it is necessary to force the fan 1 to automatically turn on the fan when it is greater than a certain temperature, set a temperature greater than 0.
;0: If set to 0, the default does not turn
;-1: Always open MF
;-2: Open when the file is printed, close when not printing EF
;[Fan 2 control]

M8030 T-1 ; 0: If set to 0, the default does not turn
; 1: 1:0 Once exposed, the fan 2 will turn, no exposure, the fan will stop LED
;-1:<0 keeps on MF
;-2: Open when the file is printed, close when not printing EF

;ˇľLED Interface Controlˇż
M8030 S4 ; 0: normally off
;1: normally open
;2: Open when the file is printed, close when not printing EF
;3: File is closed when printing, open when not printing
;4: Once exposed, the LED will turn on, no exposure, the LED will stop LED

; [SD card / U disk support folder display]
M8034 I1 ; 0: Not supported
; 1: support
;

When printing [Z demoulding, total distance of lifting height per unit, unit mm, the distance = slow rising distance + fast rising distance]
M8070 Z7; if motion z is not required, set it to 0

; [Z stripping slow rise distance] when printing]
M8070 S3; if motion z is not required, set it to 0

; [the warm-up time of the projector boot]
M8070 T10; unit is s

; [Projector communication baud rate, if you do not need serial port control, set the baud rate to 0]
M8070 I9600; projector communication baud rate

;[Projector boot command]
M8070 '* 0 IR 001\r' ; can use \r \n \t \x6e to indicate carriage return, line feed, tabulation and special characters such as hexadecimal 0x6e, up to 40 characters

;[Projector shutdown command]
M8071 '* 0 IR 002\r' ; projector shutdown command
;

;[machine type]
M8080 I0 ; 0: XYZ common type,

;
;[thermal resistance type] temperature sensor type
M8081 I0 ; 0: Ideal NTC 100K 1% 3950 B ,
;
;

;[Z zero point and limit position setting] 0: The limit position is the same as the zero point of Z: The limit position is different from the zero point of Z
M8083 I0 ; The limit position is different from the zero point of Z and needs to be used with the M8084 Z* instruction.
;
;
;; [Z limit point and zero limit difference, the value is usually positive value]
;M8084 Z0 ; If you want to set the offset in the configuration, please remove the semicolon in front of the line command, and you can also automatically configure the offset by setting Z to zero on the interface.
;
;
;[Start LOGO time]
M8085 I3000; boot logo duration, minimum 100ms, maximum 6000ms

;[Screensaver time]
M8085 T0; How long does it take to enter the screen saver interface, the unit is seconds (s), when it is 0, it means that the screen saver is disabled.

;[External Drive Settings]
M8087 I0 T0 ; I: Settling time of the direction signal to the high level of the pulse signal, in ns
; T: The minimum hold time of the pulse signal, in ns. If there is no external drive control board, set it to zero.
; Several external drive parameters: THB7128: I100000 T0 ;;;; TB6560: I40000 T0 ;;; TB6600: I100000 T0
;
;
;
;[Action after printing is completed]
M8489 P3 ; action after printing is completed
; 0: Turn off all motors,
; 1: Does not work after printing,
;2: After printing is completed, return to zero, the motor is not powered
;3: After the printing is completed, it drops to the maximum stroke of Z, and the motor is continuously powered.

;
;This parameter must not be less, otherwise the parameter cannot be saved to the device.
M8500; save configuration
;

X3msnake, 2018-10-26:
@bartwaw
Greetings Master, Photon File Editor requests should be adressed at issues on Photon File Editor Project.

Thanks for the file share and the tips on orbeat

X3msnake, 2018-11-04:
@bartwaw this orbeat file is the factory defaults for the orbeat?

can you try resin exposure finder on your orbeat?

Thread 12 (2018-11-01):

Measurements for the LED reflector

esseeayen, 2018-11-01:
I found this group and have a similar DLP printer, the wanhao d7, which we have been upgrading but someone mentioned that some of our upgrades may also be useful for the Photon. Is there any chance you can take some pictures and measurements of the space and holes for the reflector for the UV led?

Thanks!

esseeayen, 2018-11-03:
Hopefully! I that's the idea.

bartwaw, 2018-11-03:
i'm thinking about this also. But i will do it on orbeat printer.
Ordered such pcb
https://www.aliexpress.com/item/free-shipping-1pce-12W-18W-20W-24W-30W-36W-48W-Rectangle-LED-Aluminum-Plate-High-Power/32722702900.html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

which will cover whole LCD ( its 145x106 but i think that whole pcb dimension)

and 20 pcs 3W leds 405nm so they should give 60W.
But i will drive them little bit lower to get about 50w.

X3msnake, 2018-11-03:
beware that driving the leds at lower voltage may dift the led wavelenght.

what dimensions do you need?

Photon is much the same as orbeat, hardware wise so i would not be
surprised if the dimenstions are intermutable

bartwaw <notifications@github.com> escreveu no dia sábado, 3/11/2018 à(s)
15:03:

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

--
Com os melhores cumprimentos,
Vinicius Silva

esseeayen, 2018-11-04:
@bartwaw agreed, this is the reason why we were making one for the Wanhao D7, but we have done a lot of research and not just any "UV led" will do, even if it says 405nm.

@X3msnake i have attached the dimensions i need. It would be amazing if they were the same size 👍

Thanks in advance for your help.

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

esseeayen, 2018-11-04:
This was our version 1 which didn't work well, but we're onto trying something new!

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

bartwaw, 2018-11-04:
esseeayen i see that you used 5050 led's.
I've read somewhere that isn't best option.
I think that main problem is that they are almost 180 degrees.
That's why i'm thinking about such leds

https://pl.aliexpress.com/store/product/High-Power-LED-Chip-50W-UV-365nm-50-Watt-Light-Beads-UVA-Purple-COB-For-polymer/2335145_32755950096.html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

best way is to find good leds with 60 degree beam like them:
https://www.aliexpress.com/item/10PCS-Imitation-cree-led-3535-UV-LED-365nm-370nm-380nm-385nm-395nm-400nm-405nm-3W-Purple/32893869506.html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,searchweb201602_4_10065_10068_319_317_5728817_10696_10084_10083_5729417_10618_10304_10307_10820_10301_10821_5730517_5733317_5733217_10843_5733417_328_10059_10884_5732917_10887_100031_5733117_321_322_10103_5733517_5733617,searchweb201603_55,ppcSwitch_0&algo_expid=fc3b6d59-3471-4239-bab2-ecec3bd98c87-0&algo_pvid=fc3b6d59-3471-4239-bab2-ecec3bd98c87

but i didn't found aluminium PCB's that have dimensions over 120x60

anyway i'm thinking about simillar to this:
https://www.fepshop.com/shop/parts/led/paraled-3rd-party-kit/

esseeayen, 2018-11-04:
@bartwaw 5050 Leds beam spread wasn't the angle that was the issue. It's actually the lumens/watt that is the issue.

We have a solution now, but we are custom making the PCB and everything to make sure it works properly.

I know the people from FEP Shop and they said the paraled is good, but they seem to be no longer available as a DIY part, as well as being >$200!

bartwaw, 2018-11-04:
so what leds will you use ?

bartwaw, 2018-11-04:
any more :) what type

esseeayen, 2018-11-04:
you'll see :)
ᐧ

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

esseeayen, 2018-11-06:
If anyone is happy to measure, happy to provide a board for testing (free, but just pay the shipping)

madeintaiwan, 2020-03-20:
@esseeayen Did you manage to produce upgraded LED units?

Closed 2019-05-15.

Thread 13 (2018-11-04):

IWantToHelp  - gcode for mixing resin in vat

bartwaw, 2018-11-04:
Want to share my Gcode that i'm using to mix resin in VAT.
It's useful specially for colour resins - i got wanhao grey resin water washable, after one day when it stays in resin vat dye stays on bottom.

X3msnake, 2018-11-04:
what do you mean?
gcode to mix resins in the photon?

how do you achieve that?

No dia domingo, 4 de novembro de 2018, bartwaw <notifications@github.com>
escreveu:

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

--
Com os melhores cumprimentos,
Vinicius Silva

bartwaw, 2018-11-04:
Easy,
when resin stays in VAT for longer time, dye (or pigments) thanks to gravity will goes down.
This is gcode that moves z axis up and down in mixed lengths to mix resin.
It mixes resin by build platform :)
It really works on my Orbeat, which I said has same board as Photon. So i should work at 99% :)
Check it :)

X3msnake, 2018-11-04:
post it here in the issue and i will give it a try

No dia domingo, 4 de novembro de 2018, bartwaw <notifications@github.com>
escreveu:

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

--
Com os melhores cumprimentos,
Vinicius Silva

X3msnake, 2018-11-04:
missed the zip. nevermind will test it

X3msnake, 2018-11-04:
mmm, that's plaing Gcode. not sure if it will work... testing now  ;)

X3msnake, 2018-11-04:
@bartwaw @Photonsters/photonsters
https://youtu.be/M1JdoMIhdcM

looks like it does work. @bartwaw more important than the mixer, that is cool but needs to en above the endstop, where did u get the gcodes from?

do you have acess to a list of all available codes?

we can open up a page for this and respective community tool programs if you do. makes more sense that way actually.

and thanks for sharing this

X3msnake, 2018-11-04:
@bartwaw

M17 /18 is as good as not being there, compleatly ignored by the photon at least

X3msnake, 2018-11-04:
G90/91 is also ignored, printer works only in absolute coordinates

X3msnake, 2018-11-09:
@bartwaw

Can you test these codes?

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

rsilvers129, 2020-04-16:
Can you please create a mixer that will run much longer? Sometimes I run the mixer manually 10x and wish I could just have one that ran once for 15 minutes. If you think the motors will get hot, it is ok if it rests for 30-60 seconds every few minutes.

yy-cube, 2020-04-23:
@rsilvers129

You can edit this gcode with a text editor. It is really easy. Just copy & paste those mix modes (there a different types, just watch your printer when hes mixing) as often as you want / need them and you are ready to mix.

berkakinci, 2020-12-29:
Has anyone put this in gcode in the repo?  (Sorry; I'm not familiar enough to suggest where.)
I'm happy I happened across this issue.  I was about to make my own gcode.

berkakinci, 2020-12-30:
I'm attaching my takes on the resin mixing.  I made some slow and long mixes; they work with my resin vat heater.
I'm hoping these will make it in the repo as well.

[Mix Resin.zip](https://github.com/Photonsters/anycubic-photon-docs/files/5755513/Mix.Resin.zip)

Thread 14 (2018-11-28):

New Firmware Version Avaliable

trappedinalift, 2018-11-28:
It would appear that there is a new firmware available for the photon, titled V1.1_20180720
The bin file is V22_89 compared to the current V22_83

X3msnake, 2018-11-28:
yiu refering to the github files?

No dia quarta-feira, 28 de novembro de 2018, trappedinalift <
notifications@github.com> escreveu:

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

--
Com os melhores cumprimentos,
Vinicius Silva

trappedinalift, 2018-11-28:
The github bin file is V22_83 and the version on Anycubics website is V22_89. The zip file containing the V22_89 bin is titled V1.1_20180720. I haven't flashed it to my machine yet.

X3msnake, 2018-11-28:
We are only keeping old versions for safe keeping, and advising everyone to
go to anycubic website to get the latest firmware

trappedinalift <notifications@github.com> escreveu no dia quarta,
28/11/2018 à(s) 15:12:

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

--
Com os melhores cumprimentos,
Vinicius Silva

X3msnake, 2018-11-28:
yeah i forgot about this completely, will update then thanks for the heads
up

trappedinalift <notifications@github.com> escreveu no dia quarta,
28/11/2018 à(s) 16:26:

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

--
Com os melhores cumprimentos,
Vinicius Silva

Closed 2019-05-15.

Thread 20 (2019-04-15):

have purchased this machine in china in 2019 from factory and got delivered in ghungzou and then got shippment locally to pakistan , i have tested it yesterday  , it is not producing 3d form , when i am printing the block it produce which is not solid , what should i do

k3g1397, 2019-04-15:
have purchased this machine in china in 2019 from factory and got delivered in ghungzou and then got shippment locally to pakistan , i have tested it yesterday  , it is not producing 3d form , when i am printing the block it produce which is not solid , what should i do

half block remains with upside and half on downside , it breaks while printing block

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

Sailormaine, 2019-04-15:
This is my theory - no guarantees, but it might help.

I think that the resin that Anycubic is providing with the machine has changed, but the demo file has not.  I think it needs a bit more exposure.

Start the demo file again.  As soon as you have started it, press the little gear icon on the bottom right of the touch screen.  Edit the bottom setting - I think it's called "normal exposure" - and raise the value by 2 to 4 seconds.  Then click the checkmark icon and then the return icon to bring you back to the regular screen.

Let's see how well that works.

k3g1397, 2019-04-15:
Ok ill do it

On Mon, 15 Apr 2019 at 6:27 PM, Sailormaine <notifications@github.com>
wrote:

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

X3msnake, 2019-05-15:
This type os questions should be placed ate fb group not here
https://www.facebook.com/groups/AnycubicPhoton/

Closed 2019-05-15.

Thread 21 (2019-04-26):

Trouble slicing

Springcrest, 2019-04-26:
Brand new to 3D printing. I open an stl and then I hit slice. The program closes and I open the sliced file and there's nothing there. Please help

X3msnake, 2019-05-15:
Help is in the propper group channel Master
https://www.facebook.com/groups/AnycubicPhoton/

Closed 2019-05-15.

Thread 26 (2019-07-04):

Printer doesn't seem to detect the file Update.LCD

laraaj, 2019-07-04:
Hello everyone,

Anyone has any idea why the printer wouldn't update the firmware when it starts, we even tried to manually update the firmware by printing the .bin file but it doesn't work.
We tried with these two versions of the firmware :
Photon_firmware_4.2.17_beta
Photon_firmware_4.2.14
none of them is working so far, our current firmware version is : V4.2.0_LCD.0 /1440x2560 /F2.7

X3msnake, 2019-07-05:
files must be on the usb root

No dia quinta-feira, 4 de julho de 2019, laraaj <notifications@github.com>
escreveu:

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

--
Com os melhores cumprimentos,
Vinicius Silva

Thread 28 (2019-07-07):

How to make shorter supports?

Teddyz, 2019-07-07:
Is there any reason it is not possible to make the supports shorter than 3.5mm? I see no reason to waste printing-time making them taller than 1mm. Or is there a good reason for this limitation?

senkunmusashi, 2019-07-21:
The reason supports need to be a minimum distance from the build plate is to prevent pooling and curing of resin. 5mm is barely adequate to allow resin flow and refresh, 1mm and you'll get a mess of a cured resin block at the bottom of your print.

Closed 2019-07-21.

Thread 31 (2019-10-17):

Firmware GCode Query

ChessDragon136, 2019-10-17:
Good Afternoon,

With help from the documents on here I'm trying to decipher the firmware GCode settings in relation the the Z axis speed.

I have a query around M8015 and M8016 (mm/s speeds the buildplate moves up in slow phase / fast phase + down). In older firmwares, the values used are TXX, and in the newer ones PXX. Is there a difference between the T and P setting? The comments at the end of the newer version I can't translate, but appear to be defaults if value is 0?

Ultimately, I am trying to flash new timings to the Newer (PXX) version firmware, but am unsure whether to use P or T as I don't understand what the difference is.

Any help is appreciated

Thanks

Old Firmware (Yellow Version Default)
`;【Z轴脱模上升和下降速度】 脱模过程中，先慢速上升，再快速上升，然后再快速下降
M8015  T2	;Z轴慢速脱模上升速度
M8016  T2.5	;Z轴脱模快速上升及下降速度`

Newer Firmware (V4.2.12_LCDM.0 / 1440x2560 /F2.7)
`M8015  P0.9	;Z轴慢速脱模上升速度,支持小数。此处配置非0，M8015  T1自动无效，
M8016  P3.0	;Z轴脱模快速上升及下降速度,支持小数。此处配置非0，M8016  T3自动无效，`

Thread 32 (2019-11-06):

The FAQ states to find the fan_off.gcode on the Facebook group, but doesn't specify *which* group

Taegost, 2019-11-06:
The FAQ mentions that there is some gcode that can be used to shut off the fans, I can't seem to find the fan_off.gcode mentioned in the FAQ.
Can someone include a link directly to it instead?  Or better yet, pull it into the repo so it can be version controlled and easily accessible?
Thank you.

X3msnake, 2020-02-04:
photon S does not have a equivalent tool like the defaults.gcode since it
is a different board

only removing it physically

No dia quarta-feira, 6 de novembro de 2019, Mike Wheway <
notifications@github.com> escreveu:

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

--
Com os melhores cumprimentos,
Vinicius Silva

Taegost, 2020-04-29:
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

I found as much in my research, but we still need to update the FAQ with the actual code or point to where it can be found, I was never able to find it at all, and I've tried finding it for other users on Reddit that have the original Photon.

X3msnake, 2020-04-29:
gcode modifications only apply to the Photon Classic and CBD-Tech
motherboards

there  is no way to do this that we know of. contact Anycubic about it and
if you find out do share back

Mike Wheway <notifications@github.com> escreveu no dia quarta, 29/04/2020
à(s) 14:29:

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

--
Com os melhores cumprimentos,
Vinicius Silva

X3msnake, 2020-04-30:
@Taegost again, this will only work for CBD-TECH Boards > Photon Classic / Mars Classic / Orbeat / Epax X1 / Qidi Shadow / ...

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

https://github.com/Photonsters/anycubic-photon-docs/blob/master/firmware/factory-defaults-translated.gcode

X3msnake, 2020-04-30:
@Taegost Also the correct approach is to dump your printer config file istead of using the archives one since settings might vary from vendor to vendor

Open a txt file and drop these lines, change the extension to .gcode and print it in the printer (only Chitubox cbd-tech boards)

```
;ENABLE M8093 TO DUMP DEBUG TO FILE - Only works in recent firmwares
M8093 I1
```

Closed 2020-04-30.

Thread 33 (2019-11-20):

Official Update.LCD file to fix firmware upgrade problems

al31c0, 2019-11-20:
Hi, after a firmware upgrade my Anycubic Photon didn't turn on anymore, the fix dead, z-axis...file didn't work but with this file I fixed my printer. I want to share it with you.

[firmware issue.zip](https://github.com/Photonsters/anycubic-photon-docs/files/3868959/firmware.issue.zip)

X3msnake, 2019-11-20:
can you please share how did you obtained these files?

No dia quarta-feira, 20 de novembro de 2019, al31c0 <
notifications@github.com> escreveu:

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

--
Com os melhores cumprimentos,
Vinicius Silva

hellvesper, 2020-01-05:
WOW awesome! I got similar problem, and can't find any solution. But this helps, thank you!

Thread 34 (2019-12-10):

FAQ Vat Tightening issue

KroniK907, 2019-12-10:
I believe the post intends to say KHz rather than Hz. 150 - 350 Hz is the basic frequency range of a bass guitar. The snap of a snare drum falls much higher in the frequency range.

MakerMatrix, 2019-12-10:
It means what it says. The snare language is more of a metaphor so people
understand.

On Tue, Dec 10, 2019 at 2:46 AM Daniel Kranich <notifications@github.com>
wrote:

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
--
--
MakerMatrix
Please visit us on YouTube, Facebook, and Instagram

X3msnake, 2019-12-10:
It's Hz
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

Closed 2019-12-10.

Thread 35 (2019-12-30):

IWantToHelp

Chasedog98, 2019-12-30:
Updated list of known Serial Commands:
M6030 "Photon/AA-TEST-PRINTS/_ShallowAnglesAATest_0X.photon" (starts a print file name imeddiatly)
M6032 "Photon/AA-TEST-PRINTS/_ShallowAnglesAATest_0X.photon" (Reads a File Into Memory to be started with M6045) R: (file length in bytes)
M20 (List SD Card)
M23 (Select File on SD Card)
M24 (Starts printing the M6032 open file on memory)
M25 (Pause Print)
M27 (Report SD print status) (M27 S4 - Report 4 seconds, M27 S0 - Stop reporting, M27 C - Report currently open filename)
M6045 I4000 "M24" (Waits the Delay set time and Starts Printing the M6032 open file on memory)
M30 (Delete file from SD Card)
M33 (Stops print)
M106 (Turn on Fan, Only works during print)
M107 (Turn off Fan, Only works during print)
M114 (Get current position)
M115 (Firmware Info)
M4001 (returns the configured stepper movement for all axis) R: (X:0.011430 Y:0.011430 Z:0.000625 E:0.001340 T:0/0/0/155/1 U:'GBK' B:1)
M105 (returns sensor temperatures) R: (ok T:161 /0 B:164 /0 @:0 B@:0)
M8512 "configFile.gcode" (Dumps the current config.gcode EEPROM data into a file)
G28 Z (Home Z Axis)
G0 Z10 (Move Z axis at max speed)
G0 Z10 F600 (Move Z axis at F speed)
M6040 I100 (Reboot I defines the delay before restart)
M7506 I636264 T0 //0; 1; color_flip, (Changes UI colours Negative/Positive/or switch watever its on)
M9005 '"Networkname","Password"'
G90 Absolute Positioning
G91 Incremental Positioning

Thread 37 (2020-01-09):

Non-standard use of the printer

dark184, 2020-01-09:
Hello. I have a printer, ANYCUBIC PHOTON. I want to use it for more than just printing. Tell me if I can display an arbitrary image without using slicer (preferred image format *.BMP, or any other)? And turn on the lights for a few seconds?

X3msnake, 2020-01-09:
use photon file editor

No dia quinta-feira, 9 de janeiro de 2020, dark184 <notifications@github.com>
escreveu:

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

--
Com os melhores cumprimentos,
Vinicius Silva

dark184, 2020-01-09:
I found exactly what I need here
https://github.com/Reonarudo/pcb2photon
This is a Gerber to file Converter *.photon
But to my great regret it all works under Linux. Maybe there is a similar utility for WINDOWS?

X3msnake, 2020-01-09:
use photon file editor from photonsters.org.
there are other project that do similar things listed under community
projects

No dia quinta-feira, 9 de janeiro de 2020, dark184 <notifications@github.com>
escreveu:

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

--
Com os melhores cumprimentos,
Vinicius Silva

dark184, 2020-01-09:
Thanks. Installed file editor, prepared a picture in PNG format 1440x2560. Trying to upload to "file editor"... Only black screen. Am I doing something wrong?
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

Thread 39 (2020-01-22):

Updating from 4.2.17 to 4.2.18/9 causes LCD errors.

Shir0n1379, 2020-01-22:
When I perform a UV test on 4.2.17 my Photon is fine. However, if I then update the firmware to 4.2.18/9 (Anycubic or Epax) the LCD begins to flicker whenever the UV test is performed.

X3msnake, 2020-01-22:
you have a bad solder joint on the Dram.
dessoldering cleaning up and ressoldering with normal leaded solder is a
permanent fix

No dia quarta-feira, 22 de janeiro de 2020, Shir0n1379 <
notifications@github.com> escreveu:

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

--
Com os melhores cumprimentos,
Vinicius Silva

Shir0n1379, 2020-01-22:
Why does this only happen when I upgrade to 4.2.18 and fixes when I reflash to 4.2.17?

X3msnake, 2020-01-22:
Just because you dont get it with .17 does not mean it is not there.
You will end up getting frame shearing with .17 sooner or later, as soon as
you slice a model with enough checkered details to overflow the memory
buffer.

only safe firmwares are 4.0.11 (no AA) and 4.2.18 (Epax) all other
firmwares have issues

A way to test for this is filling a plate with the calibration matrix
model, slicing it and running a dry run test.

Shir0n1379 <notifications@github.com> escreveu no dia quarta, 22/01/2020
à(s) 09:41:

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

--
Com os melhores cumprimentos,
Vinicius Silva

Shir0n1379, 2020-01-22:
Okay thanks for the help, are there any videos on how to clean and resolder the Dram available?

X3msnake, 2020-01-22:
Not that I am aware of.

You need a hot air station and flux.
You first desollder the chip, and clean the contacts with good amounts of
flux, braided copper and a 40w solder iron with a flat tip
You can then proceed to solder the chip with a microsoldering tip and some
leaded solder

Similar to this video but you can use solder wire instead of paste like
they do
https://www.youtube.com/watch?v=E3OmchO_mDc

If you are not experienced in doing SMD soldering i recommend you go to
your local hackerspace or electronics guru and ask for help.

You can also try fw version 4.0.11 from photonsters fw archive. It does not
have any AA but it is a solid firmware

Shir0n1379 <notifications@github.com> escreveu no dia quarta, 22/01/2020
à(s) 12:45:

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

--
Com os melhores cumprimentos,
Vinicius Silva

Shir0n1379, 2020-01-22:
Okay not sure if this changes anything but just flashed my firmware to 4.0.11 and the same error occured

Shir0n1379, 2020-01-22:
If it helps this is the problem: https://youtu.be/uTGT1G09x-g

X3msnake, 2020-01-22:
mmm, that looks different than what i was picturing

no harm in doing the SDRAM resoldering since 90% of the graphic issues on
these boards are caused by that, but that but to be honest that is the
first time i see this issue pop up on a firmware upgrade/downgrade, usually
this show up when a screen has been damaged by pressure near the contacts
or excess heat

Shir0n1379 <notifications@github.com> escreveu no dia quarta, 22/01/2020
à(s) 13:04:

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

--
Com os melhores cumprimentos,
Vinicius Silva

Shir0n1379, 2020-01-22:
Yeh that was my original thinking when I updated I must have damaged the screen, but downgrading fixed it. Only thing I can think of is that the firmware that introduced frame-shearing actually fixed the memory overflow on my board by accident, but when frame-shearing was fixed my board started overflowing. As this also happens when I flash to the only other firmware that does not have frame shearing

Athens428, 2020-04-05:
Did you ever figure out what is causing this? I am having the exact same problem.  My screen looks just like yours after updating.

Fusseldieb, 2024-02-21:
I don't think that's a bad DRAM issue. Mine also does just this after I've updated it to 4.2.19. The display flickers now. Guess I'm going back to 4.2.17.

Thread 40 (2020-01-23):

EPAX X1 owners can update firmware to version 4.2.23

stef-ladefense, 2020-01-23:
hi,

this version is ok for original Photon ?

https://epax3d.com/pages/firmware

thx

SB

X3msnake, 2020-01-23:
yes
firmware 4.2.18 for epax X1 is currently the recommended firmware for the
photon classic

No dia quinta-feira, 23 de janeiro de 2020, Stéphane <
notifications@github.com> escreveu:

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

--
Com os melhores cumprimentos,
Vinicius Silva

stef-ladefense, 2020-01-23:
and version 4.2.23 ?

X3msnake, 2020-01-23:
no reports on .23 yet

No dia quinta-feira, 23 de janeiro de 2020, Vinicius Silva <
x3msnake@gmail.com> escreveu:

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

--
Com os melhores cumprimentos,
Vinicius Silva

Rhiker1, 2020-02-26:
I upgraded to .23 today and it worked fine so far.  One print.

m0n5t3r0u5, 2020-07-07:
> I upgraded to .23 today and it worked fine so far. One print.

Any new insights so far about the firmware?

stef-ladefense, 2020-07-07:
personally i have this firmware since january and no printing problems

m0n5t3r0u5, 2020-07-08:
Thank you . I'll try it out.

Stéphane <notifications@github.com> schrieb am Mi., 8. Juli 2020, 01:21:

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

m0n5t3r0u5, 2020-07-08:
By the way is aa active in this firmware?

Rüstem Taylan Wittig <r.taylan.akkus@gmail.com> schrieb am Mi., 8. Juli
2020, 07:31:

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

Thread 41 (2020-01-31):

How to connect wifi?

Javi-r, 2020-01-31:
how to connect wifi in eleggo mars with the module ESP8266 ?
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

X3msnake, 2020-01-31:
there is no wifi support. you can connect via ethernet.

if you need wireless get a ethernet to wifi bridge like a 15.eur vonets

No dia sexta-feira, 31 de janeiro de 2020, Javi-r <notifications@github.com>
escreveu:

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

--
Com os melhores cumprimentos,
Vinicius Silva

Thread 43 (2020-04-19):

Printed Circuit Board with a Anycubic Photon

borelg, 2020-04-19:
Hi,

I have written some steps and I slightly adjusted the PhotonCPP repo to facilitate PCB production.
If you think it might be useful to report the link in the community project, you can find it here:
https://github.com/borelg/PhotonPCB

Have a nice day,
borelg

X3msnake, 2020-04-20:
Nice
Added, Thanks

Closed 2020-04-20.

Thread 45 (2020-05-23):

LCD screen not functioning

lcanino, 2020-05-23:
Hi,

So I own an anycubic photon 3D printer. My screen star print my models with hole thought them and when I did a test the screen showed spots with black holes. I was advised to get a new screen do to the screen failing. So I went and got two ELEGOO 5.5 Inch 2K LCD. When I plugged it in it gave me two error codes T_100 and L_43. I do not know what L_43 is but I do know what the T_100. I then went and tried updating the firmware and to see if that help when that did not help I tried plugging in my back up that I got. When I installed I tried a screen test and it gave me a blank light square with no black square in the middle. I then tried to print something and got no error codes but nothing printed. If anyone has any idea how to fix this?
Any help in solving this problem would be grateful.

 Thank you in advance

X3msnake, 2020-05-25:
did you use the adapter that came with the screen and used it in the
correct position or have you simply tried to plug the straight cable to the
board?

lcanino <notifications@github.com> escreveu no dia sábado, 23/05/2020 à(s)
05:21:

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

--
Com os melhores cumprimentos,
Vinicius Silva

X3msnake, 2020-05-25:
https://www.facebook.com/Photonsters/videos/1149686608729588/

Vinicius Silva <x3msnake@gmail.com> escreveu no dia segunda, 25/05/2020
à(s) 15:50:

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

--
Com os melhores cumprimentos,
Vinicius Silva

lcanino, 2020-05-25:
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

Yes I used

lcanino, 2020-05-25:
> did you use the adapter that came with the screen and used it in the correct position or have you simply tried to plug the straight cable to the board? lcanino <notifications@github.com> escreveu no dia sábado, 23/05/2020 à(s) 05:21:
> […](#)

Yes I used the adapter and wore gloves when installing it.

Closed 2020-05-25.

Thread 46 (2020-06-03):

FAQ request - curing

dcuccia, 2020-06-03:
FWIW, I read through the FAQ and did not see any info on post-print curing boxes. Would like to learn about common OTS and DIY options, including info on LED wavelength and power. Thanks!

X3msnake, 2020-06-16:
check the main page under community projects

dcuccia <notifications@github.com> escreveu no dia quarta, 3/06/2020 à(s)
03:51:

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

--
Com os melhores cumprimentos,
Vinicius Silva

X3msnake, 2020-06-16:
As for wavelenghts you should stick to 405nm
Old fluorescent Nail Spas have a 395nm center peak but work as well albeit
a bit slower yet can cause transparent resins to yellow

Vinicius Silva <x3msnake@gmail.com> escreveu no dia terça, 16/06/2020 à(s)
11:37:

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

--
Com os melhores cumprimentos,
Vinicius Silva

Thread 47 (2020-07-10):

Off-time

Teddyz, 2020-07-10:
I just upgraded my Photon to 4.2.18 SW.

When printing I now see that it moves the platform, exposes and then has the off-time.
I was expecting, move platform, off-time and then expose.

Is it just me or is it for everyone?

I made the .photon using original slicer, then editing it and changed exposure time in Photon File Validator. Now printing...

Teddyz, 2020-07-10:
[VID_20200710_202246.zip](https://github.com/Photonsters/anycubic-photon-docs/files/4904767/VID_20200710_202246.zip)
[Ant_MM_200um_t8_o6_be60_bl3-2.zip](https://github.com/Photonsters/anycubic-photon-docs/files/4904768/Ant_MM_200um_t8_o6_be60_bl3-2.zip)

Added a film and the file I am printing, if it can help.

I was reading about off-time here: https://all3dp.com/2/anycubic-photon-slicer-all-you-need-to-know/

X3msnake, 2020-07-11:
off time always happens after the peel move it is used to add time to let
resin flow before exposing

No dia sexta-feira, 10 de julho de 2020, Dick <notifications@github.com>
escreveu:

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

--
Com os melhores cumprimentos,
Vinicius Silva

Teddyz, 2020-07-11:
Yes, that is what I want to happen.  But it does not. FW version seems to not matter. I've tested 4.2.14, 18, 19 and all seems to behave similar in this respect.

I would be glad if someone would want to test this file: [off-time_tests.zip](https://github.com/Photonsters/anycubic-photon-docs/files/4907154/off-time_tests.zip)
2plugg+2hylsa_005mm_t2_o25_be2_bl2-2.photon
Exposure time: 2s
Off time: 25s
Bottom-layer-time: 2s
Number of bottom layers: 2

On my printer, it behvaves OK for first layer.
Second layer and on: It moves platform, it waits about 16s, expose 2s, waits some 3 seconds.
Expected: Move platform, wait25s, expose 2s, wait no (or little) time.

The second file in the zip is the same, but has off-time set to 5s. It seems to wait no time after moving the platform.

Thanks for helping!
[off-time_tests.zip](https://github.com/Photonsters/anycubic-photon-docs/files/4907154/off-time_tests.zip)

X3msnake, 2020-07-12:
bottom will be considered fulfilled if the peel time is above the off time.

you can calculate what a peel time takes as value by multiplying the travel
distance by the time units

No dia sábado, 11 de julho de 2020, Dick <notifications@github.com>
escreveu:

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

--
Com os melhores cumprimentos,
Vinicius Silva

Closed 2020-10-15.

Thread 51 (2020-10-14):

Photon Workshop 2.1.23RC8 - Can't drag windo higher than top boundary of primary monitor

tlhintoq, 2020-10-14:
Let's say you have a couple monitors - maybe a second monitor on your laptop.
And monitor #2 is above #1
You can't drag Photon Workshop from the lower monitor to the upper monitor because the app stops itself from dragging.
Trying to get fancy by making your own border and title bar etc. is stopping the window from just behaving normally and as expected.

X3msnake, 2020-10-15:
Why are you posting a issue you have with Photon Porkshop here?

We are not affiliated with Anycubic nor have we been involved with the development of Porkshop

You should contact anycubic

Closed 2020-10-15.

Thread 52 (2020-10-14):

MonoX (Mono-x) raise height after job complete is very low

tlhintoq, 2020-10-14:
When the new MonoX completes a job, it raises the plate about 15-20mm.
That's not a lot. So after every job the user has to raise it manually on the touchscreen  Very user UNfriendly.

Can the bed be raised to nearly the top just like the older Photons? Leaving plenty of working room?

X3msnake, 2020-10-15:
you will have to ask Anycubic we since they use their own board and have no
tools available

tlhintoq <notifications@github.com> escreveu no dia quarta, 14/10/2020 à(s)
19:52:

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

--
Com os melhores cumprimentos,
Vinicius Silva

Closed 2020-10-15.

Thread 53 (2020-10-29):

Is there a way to level without touchscreen?

TheTh1rt33nth, 2020-10-29:
Hello to photon users! Is there a way to home photons without touchscreen? Maybe via usb or so
My touch screen is not working in right-down corner, so i can not press the "back" button and therefore level the bed. I hope there is an alternative way to do this

X3msnake, 2020-10-29:
wierd. touchscreen fail mode is not usually like that. try using a allen key to gently press the back button.

there is a number of actions you can perform via universal network sender, like uploading and managing prints and print files. and you can also do that via serial

if you mean levelling as in setting zero offset. that command however is not available afik

but if you mean home, the command can be sent via terminal with a G28 Z

if you have a Esp8266 you can install it permanantly inside your case with esplink firmware and use the terminal to send command accessing it via your web browser

X3msnake, 2020-10-29:
list of commands can be found on the blueprint folder of this documetation project

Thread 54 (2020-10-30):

Downgrade from .19 to .18 issue

kahl, 2020-10-30:
I have tried to downgrade from 4.2.19 to 4.2.18 but I can run the .18 bin OK while the .18 LCD gives me "Unknown file format". Is the LCD necessary given the fact I have installed already the .19 LCD?

X3msnake, 2020-11-21:
should be ok

but check if you are not trying to run a mac hidden .file instead of the
real file

No dia sexta-feira, 30 de outubro de 2020, kahl <notifications@github.com>
escreveu:

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

--
Com os melhores cumprimentos,
Vinicius Silva

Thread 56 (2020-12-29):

#IWantToHelp - Anycubic Photon Firmware <-> Chitubox slicer setting correlation experiment

berkakinci, 2020-12-29:
#IWantToHelp

I ran an experiment to correlate Chitubox (v1.7.0) slicer settings with Anycubic Photon Firmware (4.2.19.3) behavior.  I thought I'd share the results for others' benefit.  Please insert the below in the repo in a place that makes sense to you.

### Anycubic Photon Firmware <-> Chitubox slicer setting correlation experiment

I was scratching my head about what exactly the "settings" changed.  I couldn't find satisfactory answers online, so I had to do an experiment.

###Method:
In Chitubox: put a model far off the build plate.  Model is off the plate because I had resin in the vat, so I did't want it curing.
Make a bunch of .photon files with different combinations of settings; with file names like "E_50,2,2,5,0,0 15,10,65,65,150.photon"
Record video of running the first few layers of each file and go back and try to make sense of stuff.

###Results:
I'll try to list what I found, but first, the "anatomy" of a layer print on the Anycubic Photon.  These are "instantaneous time points" I'll use later:
1. Start Layer exposure
2. Finish Layer exposure
3. Start move slowly away from screen
4. Start move quickly away from screen
5. Start move quickly back toward mask
6. Arrive at next layer Z
7. Start Layer+1 exposure

Here is the settings screenshot for the file "E_50,2,2,5,0,0 15,10,65,65,150.photon":
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

I hope the "bottom" layer stuff is self explanatory; it's just special set of parameters for the first few (2 in this picture) layers.  I didn't scrutinize the transition between bottom to normal layers.
One exception: "Bottom Light-off Delay" doesn't seem to do anything.

Here are the more difficult-to-understand (IMO) settings:
- Light-off Delay: This is the time between time-points #2 and #7 above.
- Lift(ing) Distance: This is the total Z distance traveled away from the screen between layers.  It's traveled between time-points #3 to #5.
- Lift(ing) Speed: This is the Z speed between time-points #3 and #4.
- Retract Speed: This is the Z speed between time-points #4 and #6.

 Now I see the biggest source of my confusion: There is no setting for the distance traveled between time-points #3 and #4.  It seems "hardcoded" at 2.5mm (my estimate).

I was messing with these settings because I can clearly hear the layer doesn't separate from FEP film in those 2.5mm.  Now I see why my messing was in vain.  I suspect there are M8xxxx gcodes for that distance.  I'll start looking in Photonsters repo.

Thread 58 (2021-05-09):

USB read issues

Guthur, 2021-05-09:
Hi

I just wanted to share my theory on the common USB read errors with some of the AnyCubic models.

I had issues where it would not read Lexar USB sticks at all and from what I gathered AnyCubic recommend using <8GB sticks, mine was 16GB.

But I don't actually believe it's the capacity itself as I have now got a SanDisk 16GB to work.

The reason I selected the SanDisk was due to having read an number of reports that the +5V line on the USB interface is sometimes relatively low and so I started to believe that there maybe a power delivery issue and SanDisk appears to have relatively low power consumption.

I think this is why <8GB is recommended and may often times work more reliably as it's likely got less power draw on average.

I'm not sure if we could figure out some mod to provide more reliable power delivery to the USB, or potentially use a USB drive that has external power supply (I've not tried this and it would be less convenient than a flash drive anyway).

X3msnake, 2021-05-09:
did you measure the power supplied to the USB and confirmed this to be a
issue?

Michael ***@***.***> escreveu no dia domingo, 9/05/2021 à(s)
04:19:

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

--
Com os melhores cumprimentos,
Vinicius Silva

Guthur, 2021-05-09:
@X3msnake I've not got the equipment to do so at the moment, I'm basing a number individuals who have measured it.

I'll try to get hold of something to measure it.

X3msnake, 2021-05-10:
Would be interesting to know if this is the case.

Michael ***@***.***> escreveu no dia domingo, 9/05/2021 à(s)
07:26:

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

--
Com os melhores cumprimentos,
Vinicius Silva

ChronoDK, 2021-12-19:
I got my USB working by formatting with this tool: https://rufus.ie/en/
Select non-bootable, MBR, FAT32.

mattwithoos, 2022-05-18:
**TL;DR: This is extremely unlikely to be the cause, see @ChronoDK 's comment.**

Stumbled across this by accident. I have a faulty Photon Mono X and can (perhaps) rule this theory out, at least for the X.

As the USB spec tolerates +-5% under load, a problematic "low voltage" would be anything under 4.75v. I note a stable 4.98v at rest and under load, but respect that others may have different readings for different models and under different loads for different motherboards.

Honestly, given @Guthur doesn't mention what formatting was factory-applied to the Lexar thumbdrive, I theorise that Lexar drives come preformatted to GPT, which is obviously incompatible - the docs advise formatting to MBR. Tangential evidence online suggests Lexar thumbdrives come preformatted as GPT - https://superuser.com/questions/1438615/usb-drive-not-working

Further, the power draw of a thumb drive is not worth even thinking about. We're talking tiny milliamp ranges, with a max (afaik) of 100mA before you need to write complex firmware logic to request more voltage from the host. You'd likely see other major issues elsewhere if power delivery was so poorly designed that they failed on the USB spec. It's just really unlikely and an unfair assumption to cast doubt over the circuit designers' efforts.

While I don't think I need to say more, the original post contains a lot of hearsay, so I'll share this: https://www.researchgate.net/figure/Power-consumption-of-all-devices-idle-read-write-under-USB-11_fig1_4361182 - this not only categorically rules out that the power consumption is a concern, but also completely refutes @Guthur's key assertions on SanDisk's alleged quality. Namely:
a) SanDisk are NOT more efficient (open to being corrected, can you link where you read this?)
b) SanDisk are actually the **worst** offenders for power consumption

In fact, as their storage goes up, they use more power! So unless the theory is that more power consumption by the USB supported by a high-quality power delivery system is the culprit (which would make it an oxymoron), I think we can rule out the USB port.

I think the nail in the coffin is @ChronoDK 's confirmation that USB read issues were resolved by formatting it as per the docs, which is also the standard advice throughout the community, and also advice which seems to work.

It may make sense to close this issue to not confuse future readers, unless @Guthur is happy to share:
 * A link to the power draw of a SanDisk USB, and a couple of comparable comparison USB powerdraws
 * A link to the discussion where all these "individuals who have measured it" shared their results

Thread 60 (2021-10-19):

#HelpMeHelpYouHelpUsAll

cab404, 2021-10-19:
Hello, I currently maintaining SL1toPhoton and pyphotonfile repos. I actually need some help to add support for "*.photons" and "*.pws" files -- as I suspect you have a good park of printers in your community, and I only have a Fauxton.
Can you add me to Slack?

X3msnake, 2021-10-20:
easyest way is to use UV3DP command line conversion tool or UVTools command
line.

what is your slack nick? do you have Facebook?

No dia terça-feira, 19 de outubro de 2021, Vladimir Serov <
***@***.***> escreveu:

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

--
Com os melhores cumprimentos,
Vinicius Silva

cab404, 2021-10-20:
Nope, I don't have facebook. Slack email: me@cab404.ru.

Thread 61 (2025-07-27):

Connecting an original Photon 5.5 via ethernet

Pintokitkat, 2025-07-27:
I applied the updates and everything seemed to go well.  The UI screen is now blue on black, which is MUCH more readable.  The network tool is also available.  When I connected an ethernet cable to the Photon motherboard and my network, the printer acquired an IP address.

But in Chitubox, when I run the Manager to setup the printer, it isn't found.  ChituManager just looks and looks, but gets nowhere.  I tried wifi, but can't find a way to enter the SSID and password, so went back to ethernet.  Same result.

What am I missing?

Thanks.

Andy

X3msnake, 2025-08-10:
https://github.com/Photonsters/Universal-Photon-Network-Controller/blob/master/README.md

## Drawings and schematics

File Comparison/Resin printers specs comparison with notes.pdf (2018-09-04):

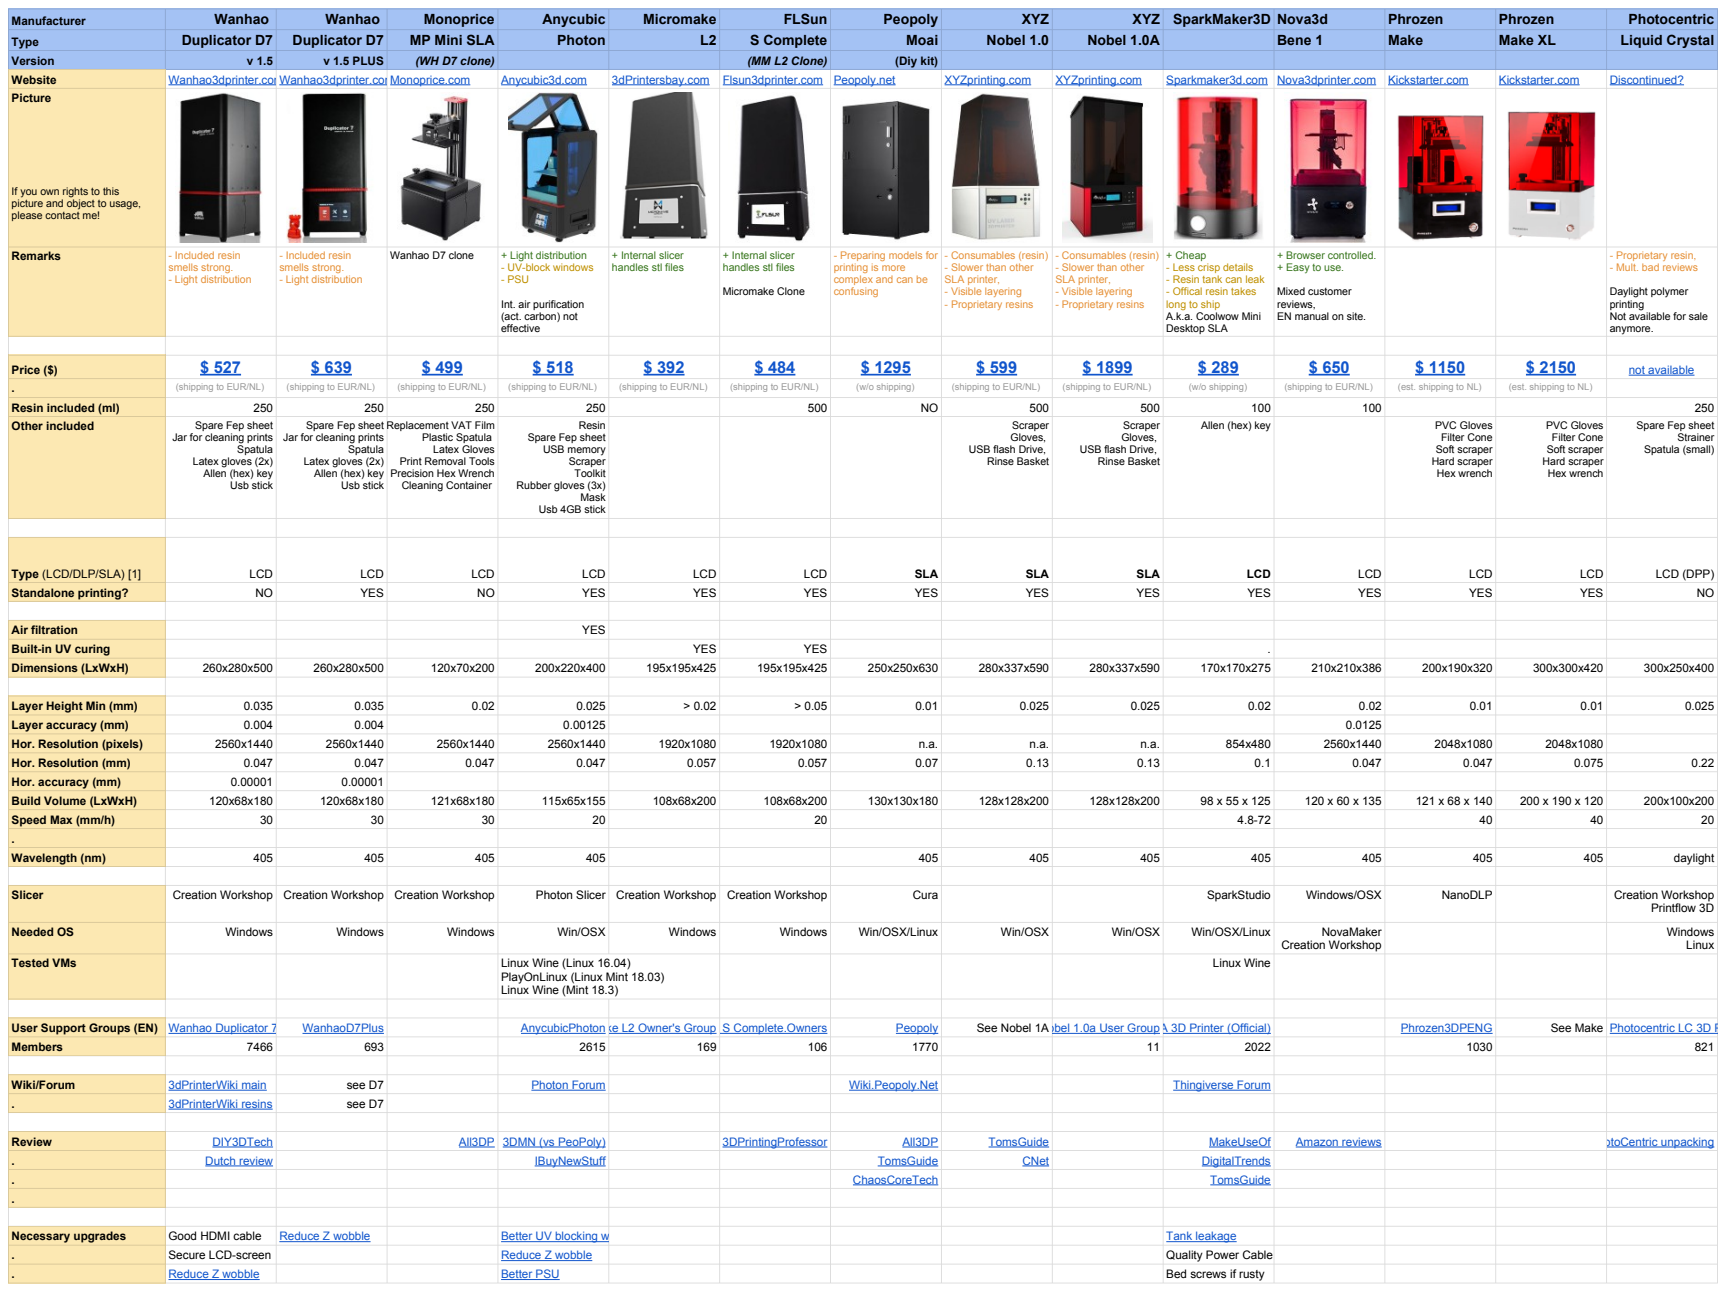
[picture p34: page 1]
Manufacturer; Wanhao; Monoprice; Anycubic; Micromake; FLSun; Peopoly; XYZ; XYZ SparkMaker3D Nova3d; Phrozen; Photocentric; Type; Duplicator D7; MP Mini SLA; Photon; S Complete; Moai; Nobel 1.0; Nobel 1.0A; Bene 1; Make; Make XL; Liquid Crystal; Version; v 1.5 PLUS; (WH D7 clone); (MM L2 Clone); (Diy kit) Website; Wanhao3dprinter.comWanhao3dprinter.comMonoprice.com; Anycubic3d.com; 3dPrintersbay.com; Flsun3dprinter.com Peopoly.net; XYZprinting.com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

If you own rights to this picture and object to usage, please contact me!

- UV-block windows
- PSU

+ Internal slicer handles stl files

- Preparing models for printing is more

- Consumables (resin)
- Slower than other SLA printer,

+ Cheap
- Less crisp details
- Resin tank can leak
- Offical resin takes
long to ship A.k.a. Coolwow Mini Desktop SLA

+ Browser controlled. + Easy to use.

- Proprietary resin,
- Mult. bad reviews

complex and can be
confusing

Int. air purification
(act. carbon) not effective

Mixed customer
reviews, EN manual on site.

Daylight polymer printing Not available for sale anymore.

Spare Fep sheet
Jar for cleaning prints Spatula

Replacement VAT Film
Plastic Spatula Latex Gloves Print Removal Tools Precision Hex Wrench Cleaning Container

Resin Spare Fep sheet USB memory Scraper Toolkit Rubber gloves (3x) Mask Usb 4GB stick

Scraper Gloves, USB flash Drive, Rinse Basket

PVC Gloves Filter Cone Soft scraper Hard scraper Hex wrench

Spare Fep sheet Strainer Spatula (small)

Latex gloves (2x) Allen (hex) key Usb stick

[1] DLP uses an array of mirrors and a light column to project an image. LCD uses an screen to mask/block parts of a light column.
SLA uses a laser to draw an image.

# (LCD is often wrongly denoted as DLP)

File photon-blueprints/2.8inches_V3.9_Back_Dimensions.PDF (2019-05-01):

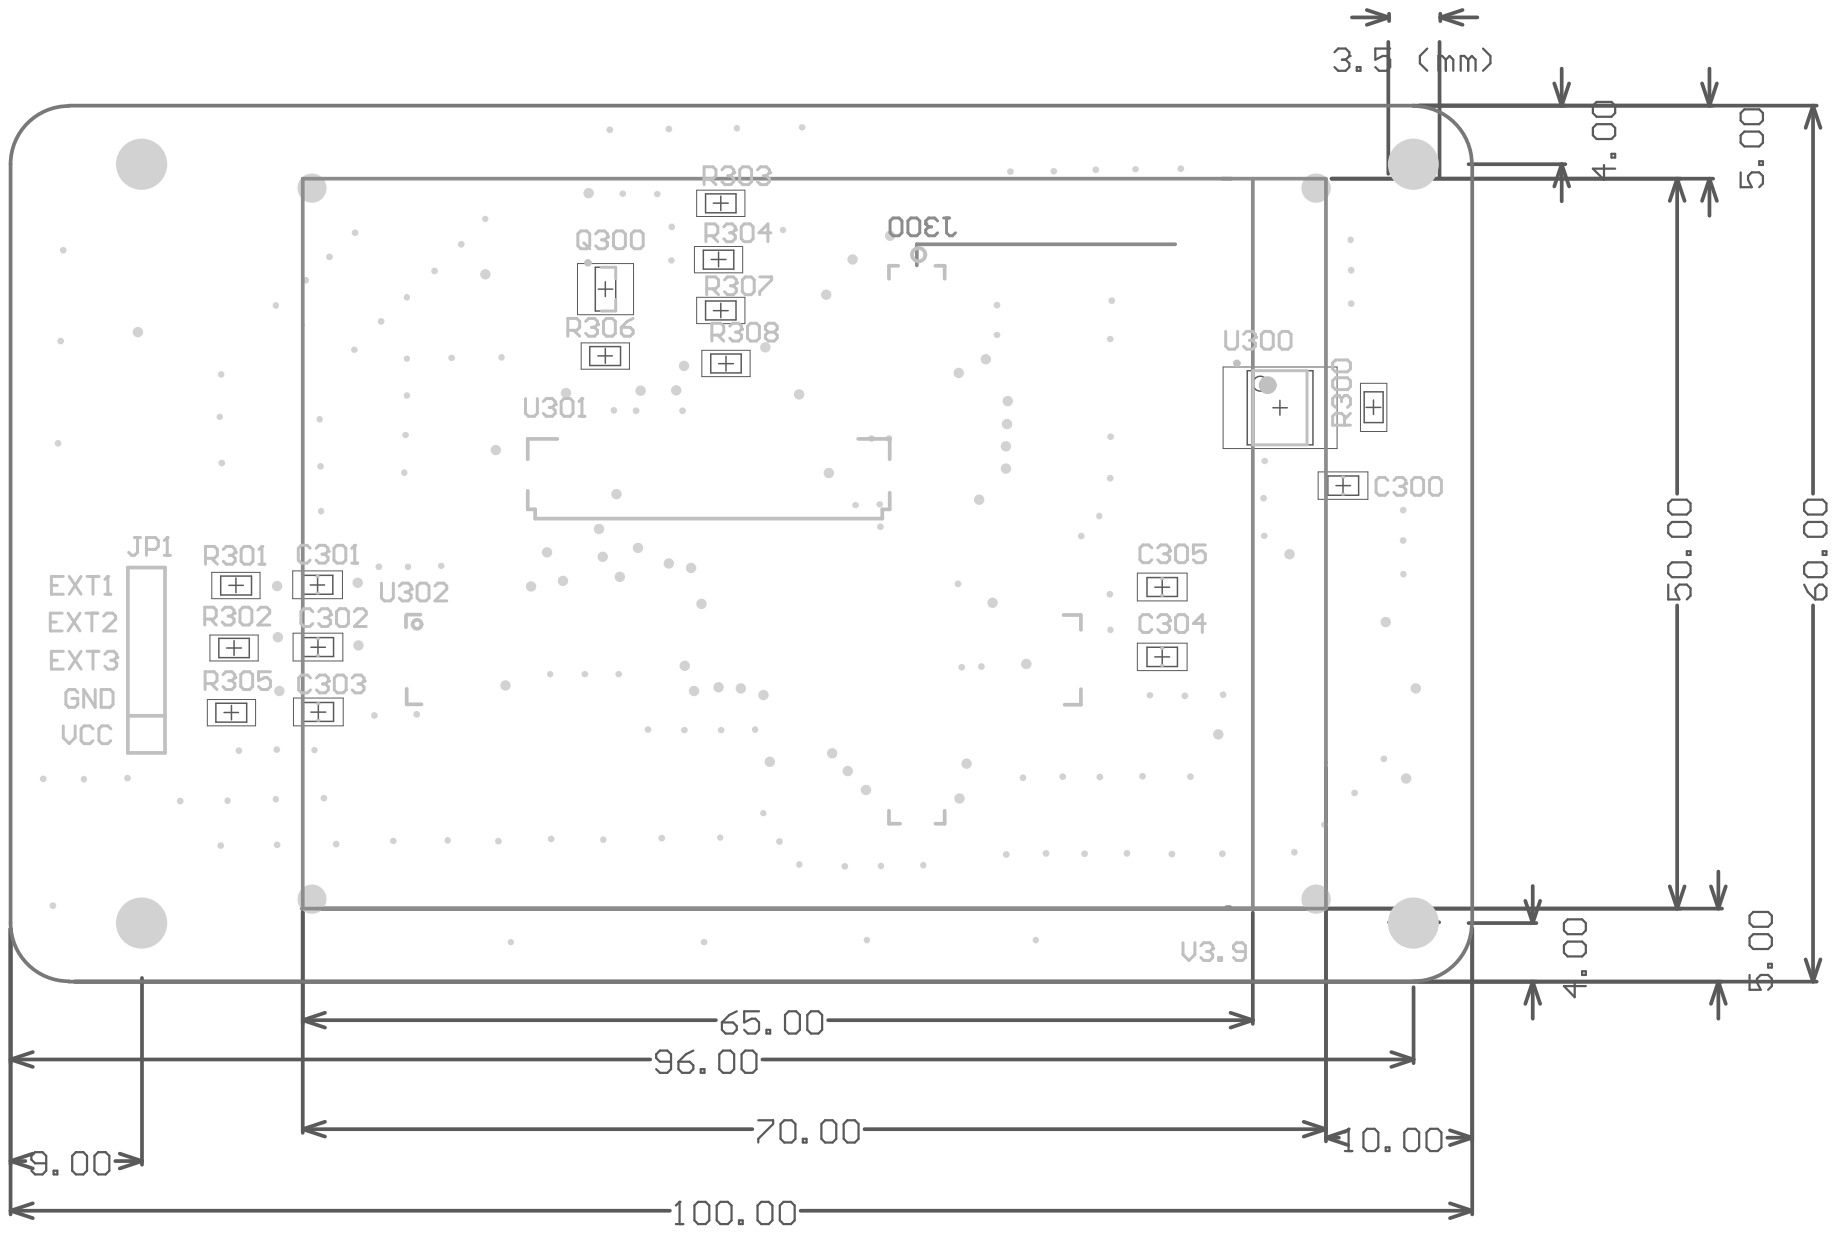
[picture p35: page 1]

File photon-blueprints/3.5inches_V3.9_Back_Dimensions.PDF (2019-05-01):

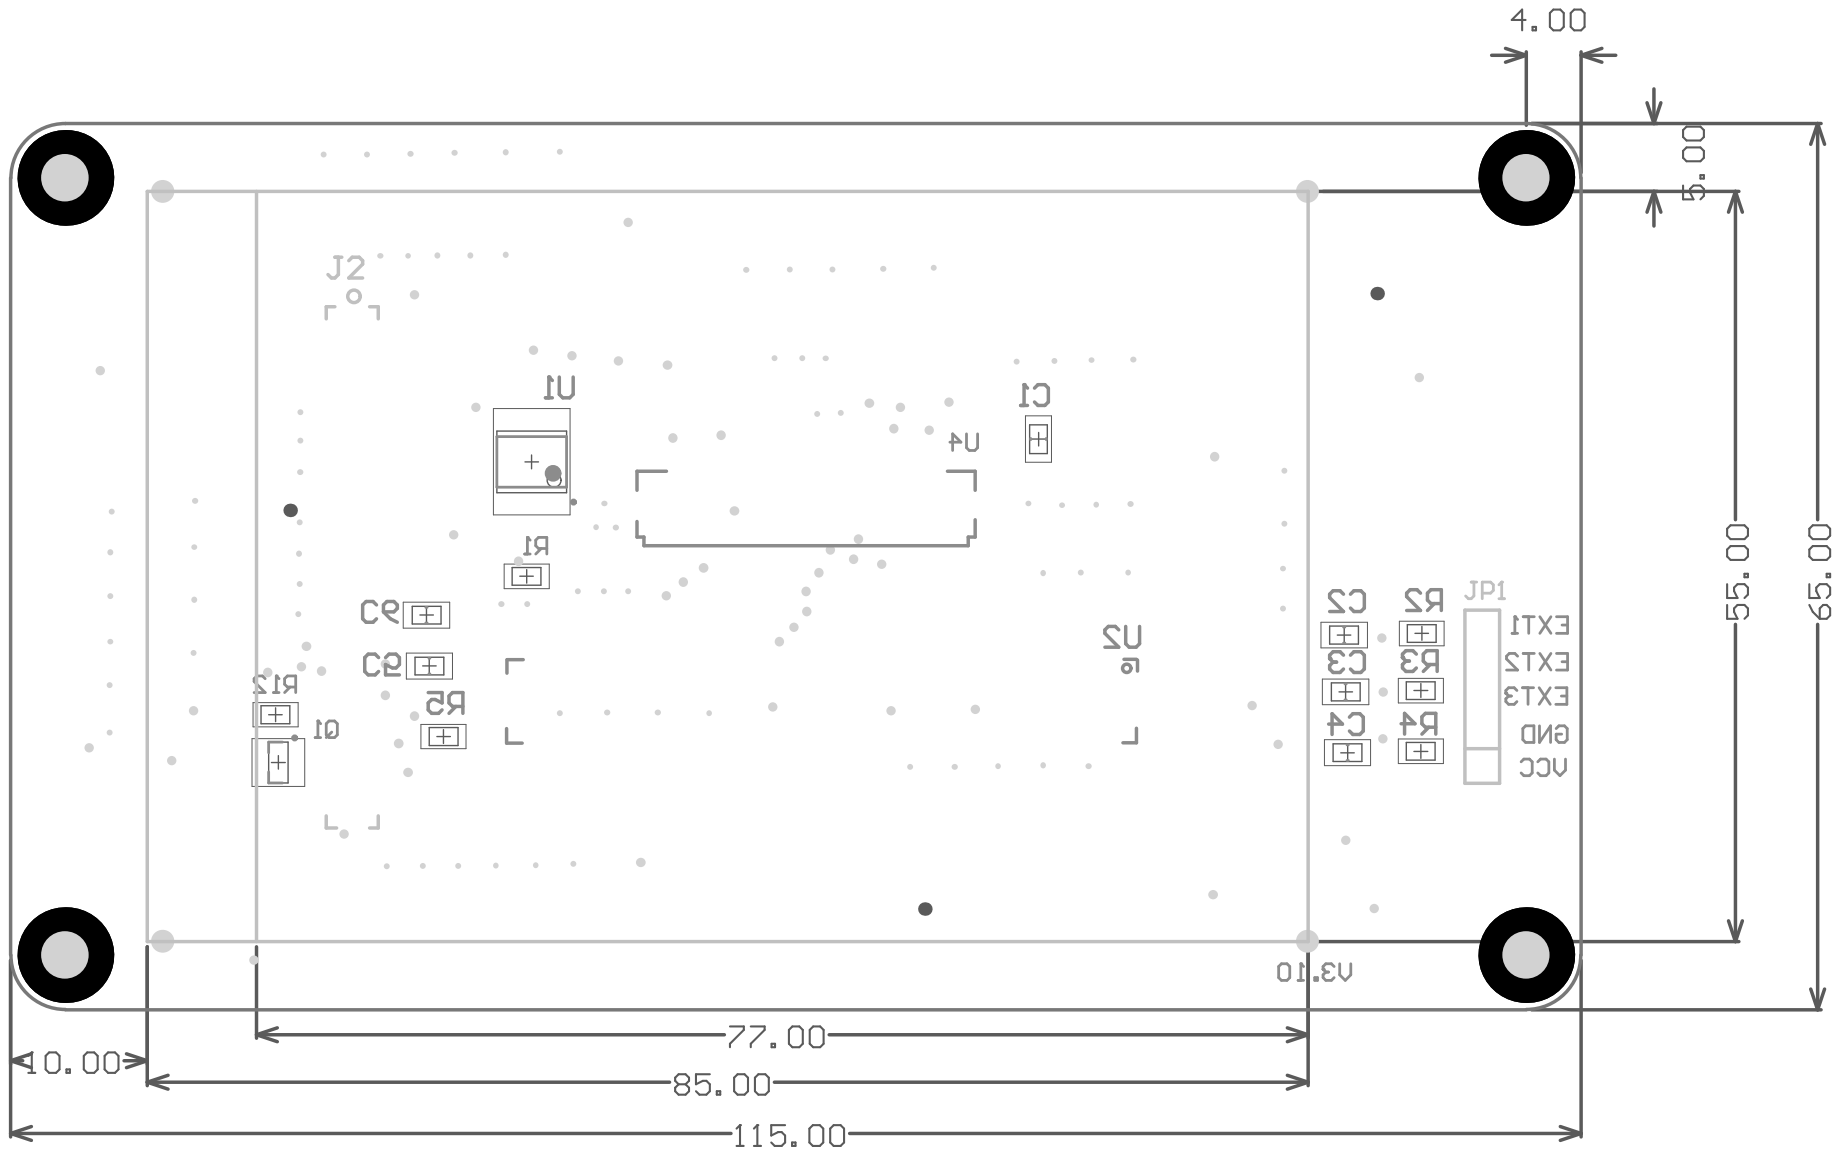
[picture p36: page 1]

Comment | Description | Designator | Footprint | LibRef | Quantity
104 | | C1, C2, C3, C4, C6 | 0805_SMD_C | CAP NP | 5
106 | | C5 | 0805_SMD_C | CAP NP | 1
ILI9481_3_5_LCD_37P | | J2 | LCD_37P_1mm | ILI9481_3_5_LCD_37P | 1
JP_5P | | JP1 | SIP5 | JP_5P | 1
S9014 | | Q1 | S9014-SOT-23 | S9014 | 1
10K | | R1, R2, R3, R4 | 0805_SMD_R | R | 4
0R | | R5 | 0805_SMD_R | R | 1
1.5K | | R12 | 0805_SMD_R | R | 1
ADS7834/XPT2046_1 | | U1 | SOP_XPT2046-8N | ADS7834/XPT2046_1 | 1
FPC_40P_1MM | | U2 | FPC_40P_1MM | FPC_40P_1MM | 1
FPC_40P_0_5MM | | U4 | FPC_40P_0_5MM | FPC_40P_0_5MM | 1

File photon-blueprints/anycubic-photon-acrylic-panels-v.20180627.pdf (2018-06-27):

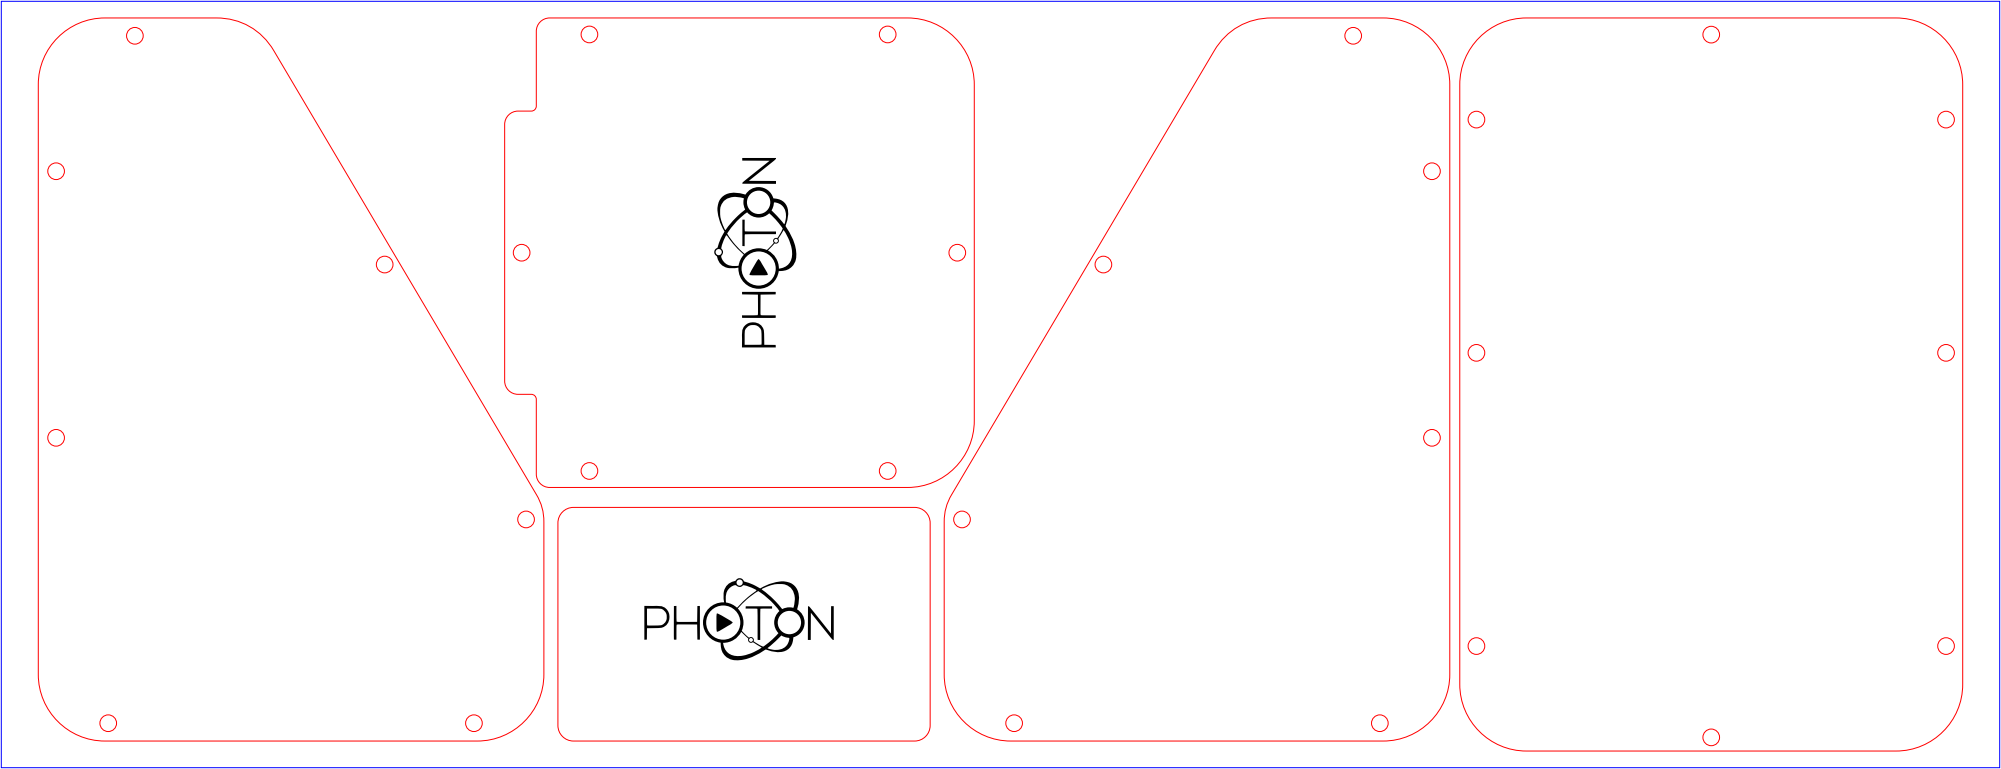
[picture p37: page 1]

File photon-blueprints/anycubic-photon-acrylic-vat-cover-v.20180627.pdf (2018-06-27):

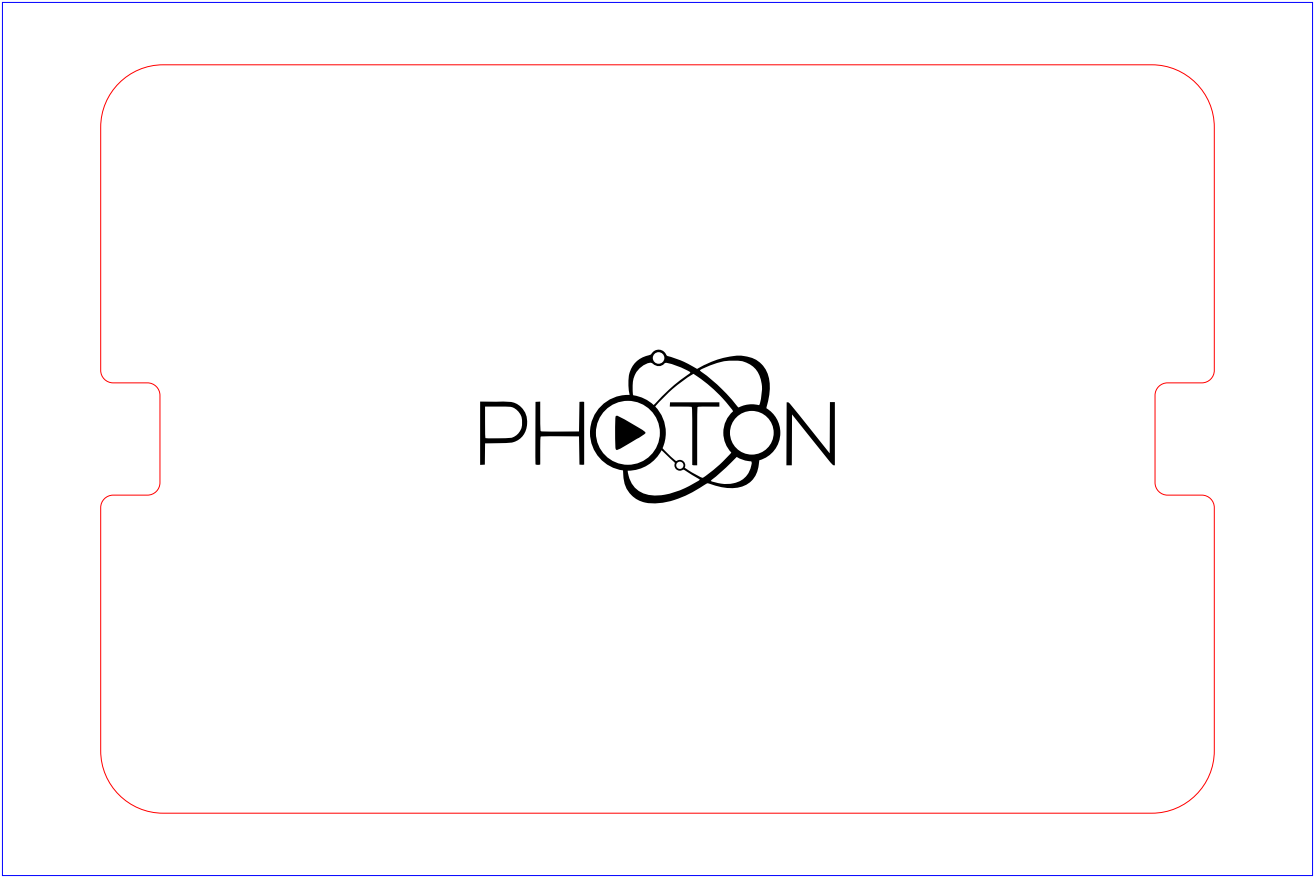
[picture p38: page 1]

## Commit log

2018-06-29 added cool STL model references
2018-07-18 Photos of dissambled print mount
    Some resin might enter causing loose printhead.
2018-08-04 Added new folder for experimental dev models
    First commit has Ivan gyroid fill pattern bust print
2018-10-18 Photon psu comparison photo
    1st version supplied with early Photons, blue windows.
    2nd version supplied with earlier yellow windowed Photons, also some late blue windowed Photons.
    3rd version supplied with current yellow windowed Photons (as of Aug 2018.)
2018-10-24 Kudos Curtis Miller
2018-11-19 Add files via upload
    "Not a Cube"
    (quick calibration test model)
    Quick test for Z wobble, or other surface anomalies.
    Can be used for dimensional accuracy tweaking.
    Quick 2 hour print, 0.05 layers, standard settings for anycubic green.
    Other resins or layer heights, times will vary.
    Saves on resin too!
    Print flat to build plate, no supports.
    Do not rotate.
    Base is 30mm diameter.
    Walls are 20mm x 20mm.
    Needle is 4mm, 2mm, 1mm.
    [notacube_01a.stl]
2018-11-22 Add files via upload
    "Nest a Cube"
    Quick test for dimensional accuracy tweaking.
    Use this to dial in resin tolerances for parts that are meant to fit together, pegs, etc.
    Quick 1 1/2 hour print, 0.05 layers, standard settings for anycubic green.
    Print cubes as is. Slice and print.
    Sleeve cube is 10 x 10 x 10mm.
    Walls are 1mm.
    Solid nesting cube is 7.8 x 7.8 x 8.9mm.
    Tweak exposure settings until the solid cube can slide into the sleeve cube snugly. Sleeve cube has a hole on top so you can push solid cube back out.
    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
    [nestacube_10mm.stl]
2018-12-26 Update FAQ.md
    Added exposure times for sample green 0.05 layers.
2019-01-14 Added more detailed info to FEP Tensioning
    Why it should be set between 250-375 and not higher/lower
2019-01-16 Update FAQ.md
    Rephrased under Printing.
2019-01-17 Update README.md
    Mask boundary check file moved under calibration models header.
2019-04-13 decreasePixel was reported to damage printer
    Seems to set lift distance to 0, fusing the build plate into the LCD.
2019-05-01 Screen sizes and BOM taken from ChituClient
2019-05-01 Covers for CBD LCD screens taken from ChituClient
    [lcd_cover_2.8.STL, lcd_cover_3.5.STL]
2019-06-05 Dead z axis and fans issue and fix
2019-07-04 added endstop ref
    kudos mike
2019-07-04 Add files via upload
    Spreadsheet of all fastener sizes/threads used on the original Photon
    [Anycubic Photon Fasteners Sheet.xlsx]
2019-07-04 Update readme.md
    added link to CAD model on GrabCAD
2019-07-09 Fonts from SPI memory
    Fonts extracted form SPI memory. Used for text boxes and file names.
2019-07-22 Disconnect Smell Distributor™
2019-07-24 Photon firmware v4.2.19 (AA) frame shearing fixed
2019-08-31 Note Flint method pressure damage.
2019-10-08 Pulseview recording of a good stepper driver
2019-11-06 Fix inverted UI colours. Unzip and Print from usb
2020-01-12 Definition loss underside prints, graphic.
2020-03-20 Proper FEP tensioning, link.
2020-05-04 Chitubox boards are using makerbot makerware?
    searching the web for Makerware退丝长度 that was dumped on the sonic mini eeprom we found this link
    https://cdn.thingiverse.com/assets/64/a2/70/e6/86/CHITU_FIRMWARE_COMMANDS_CHINESE_V1.4.0.txt
2021-04-20 This command sets the led behaviour
    read on a notepad to see the options
